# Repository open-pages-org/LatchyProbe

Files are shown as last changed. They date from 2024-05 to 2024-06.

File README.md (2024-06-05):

# Latchy Probe

A 3D printable alternative to the Omron TL-Q5MC2 inductive sensor commonly used on FDM printers for bed leveling.

Having a printer with no auto bed leveling is frustrating. While BL-Touch is a common choice, inductive probes are simple off-the-shelf items. Klicky and Unklicky probes can be printed but need magnets. What if there was an alternative that you could easily print and only needs a few parts that you probably already have?

The inspiration for this is the Klicky probe (and other similar devices) that have led the way. The objectives for this project are almost identical to the Klicky objectives [here](https://github.com/jlas1/Klicky-Probe/blob/main/README.md).

All the details, instructions and printable parts for the Latchy Probe are shared [here](https://github.com/open-pages-org/LatchyProbe) in Github, contributions to the project are welcome.

LatchyProbeVideo (https://www.youtube.com/watch?v=6NL-_C0w8O0) 

## Objectives
- Drop-in replacement for Omron TL-Q5MC2 or PL-08N2 (no need to replace the toolhead)
- No soldering required
- Minimal adjustments required
- Detect all print surfaces
- Close to the hotend tip
- Highly repeatable and accurate
- Less temperature variation
- No melting of parts
- Cheap to build
- Reuse spare parts if possible

## Additional Features
- Uses common items found at home, no special parts needed
- Does not reduce the printable area
- No detachable parts

The Latchy Probe has been developed over many months, with dozens of prototypes and 3 full test versions. It has been tested on a Creality CR10 (my Voron is still in the pipeline) and works well. The design is optimized for FDM printing but can be miniaturized using resin printing. Feedback is always welcome here or on Discord (crashysmashy1).

If you want to support this project, please consider donating [here](https://paypal.me/CrashySmashy?country.x=GB&locale.x=en_GB).

## Presenting the Latchy Probe
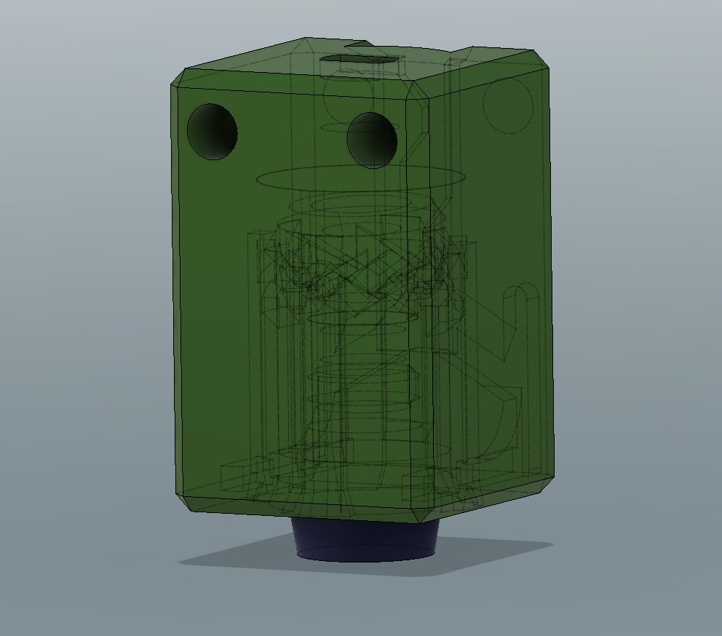
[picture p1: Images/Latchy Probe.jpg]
Latchy Probe


Latchy Probe is a direct size-for-size replacement for the Omron TL-Q5MC2 inductive probe, allowing it to use the same mounting points and adaptors for many printers.

### Features
- Physical contact switch of the same size as the inductive probe
- Deployed using the 3D printer’s motion system, like Klicky
- Similar internal contacts to Unklicky, but without detachable parts
- Probe tip retracts when not in use, similar to BLTouch
- Cheap, accurate, and can be built at home using parts from a retractable pen

Electrically, it uses only 2 wires that can be connected to the probe input on controller boards, with no external signals or power connections needed. The probe circuit is fail-safe, as it has a normally closed circuit when correctly deployed.

### Deployment
The probe is deployed by pressing the tip down onto a small post located on the printer frame to release the latch. 
- For a bed slinger the post can be at one end of the X axis.
- For Core XY the post can be near the Z homing pin.
The trigger post can be rigid or flexible, a flexible post allows for accidental horizontal contact between the probe and the post without incident.

Macros allow the deployment process to be automated. Example macros for deployment and retraction moves are provided [here](Macros/README.md). If the probe is not deployed before use, the probe circuit will remain open, and standard Klipper macros will report "Probe is already triggered" and stop.

## Building the Probe

### Parts Needed
- 3D printed parts
- Spring from a retractable pen, more details [here](#finding-a-spring)
- Thick copper wire for contacts (1.3mm diameter, 16AWG, 17SWG, or 18SWG)
- Connection wiring
- Mounting screws

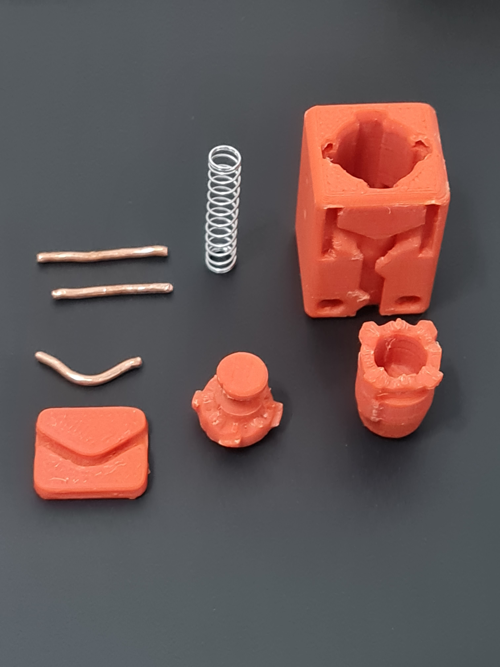
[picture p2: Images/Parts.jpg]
Latchy probe parts


### Printing the Parts
Ensure your printer is well-tuned to avoid issues like stringing, layer zits (if needed, paint the z seam into recessed corners), blobs, elephant foot, and over extrusion. 

Use the following settings:
- Print speed: Slow print speed with sufficient cooling
- Layer height: 0.1mm or 0.15mm
- Nozzle: 0.4mm (or finer if available)
- Material: ABS or ASA
- Supports: Not required
- Perimeters: 3
- Top/Bottom Layers: 5
- Infill: 15%

Parts to print:
- Probe Case (select the case to suit the available wire size)
- Probe (select the probe to suit the available wire size)
- Probe Latch
- Trigger Post, more details [here](#Trigger-Post-and-Mounting-Brackets)
- Optional bending and cutting jig for the cross pin

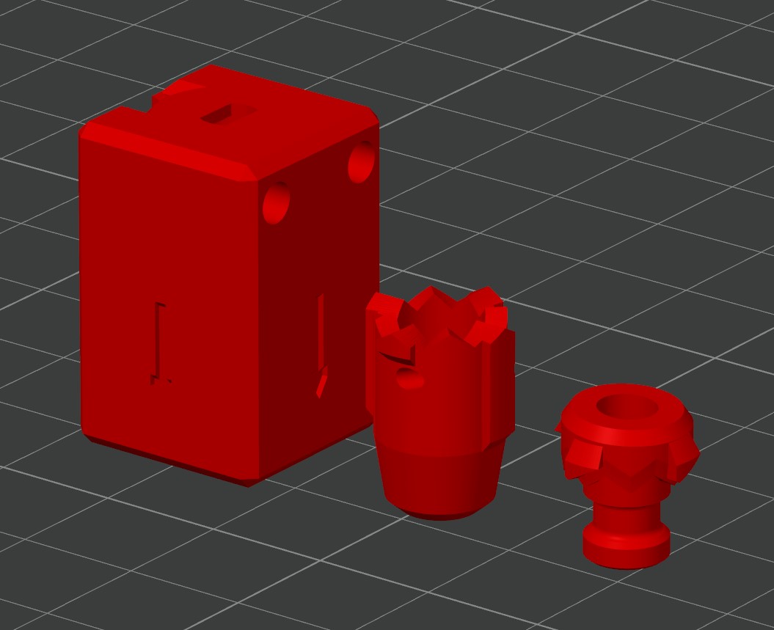
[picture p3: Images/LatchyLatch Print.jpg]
Latchy 3D prints


### Finding a Spring
- Spring diameter: 3-4.5mm (ideal size: 4.25mm)
- Spring length: approximately 23mm free length and 7mm compressed
- Spring force: 0.35mm wire diameter

If the spring is too soft the contacts will not be reliable. If the spring is too stiff it will displace the bed surface when probing giving inaccurate readings.

### Assembly
1. Cut 3 lengths of copper wire approximately 15mm long. Bend 1 piece to match the profile of the jig and trim the ends flush with the jig. Ensure there are no burrs and round the ends with a file if needed.

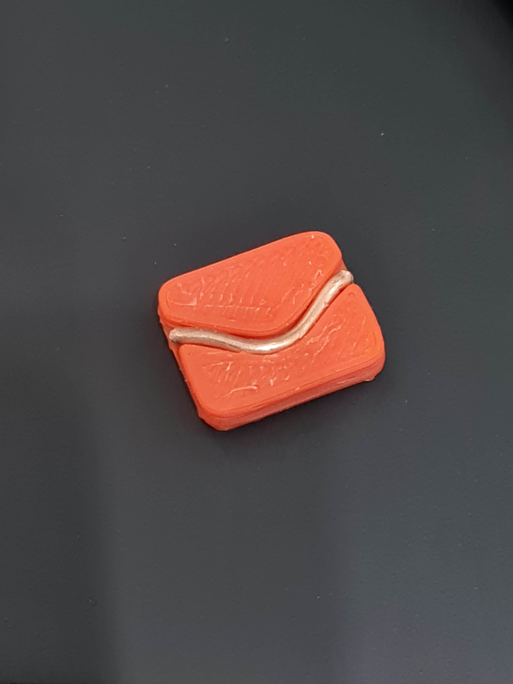
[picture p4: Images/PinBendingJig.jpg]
Pin bending jig


2. Insert the latch part into the probe part; the latch should rotate freely, bumping up and down on the ramps.

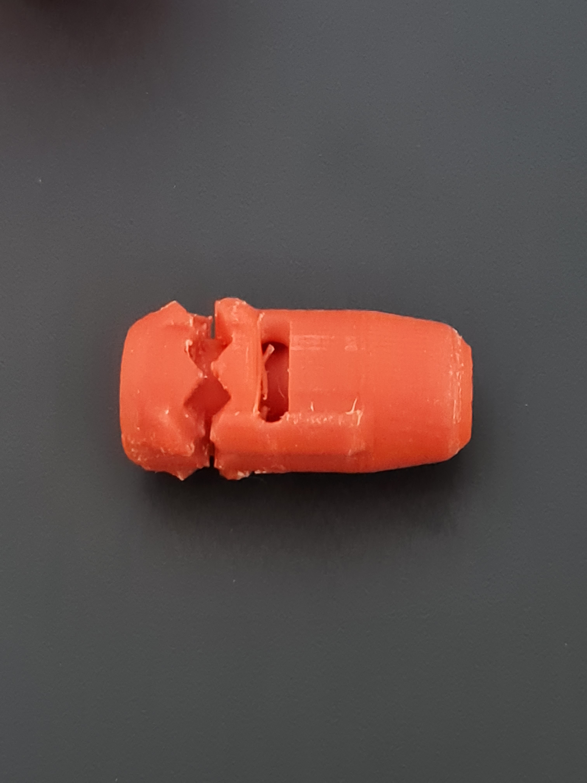
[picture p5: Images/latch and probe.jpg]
Latch and probe


3. Insert the copper cross pin (this retains the parts and forms the electrical contact). The latch should still rotate freely.

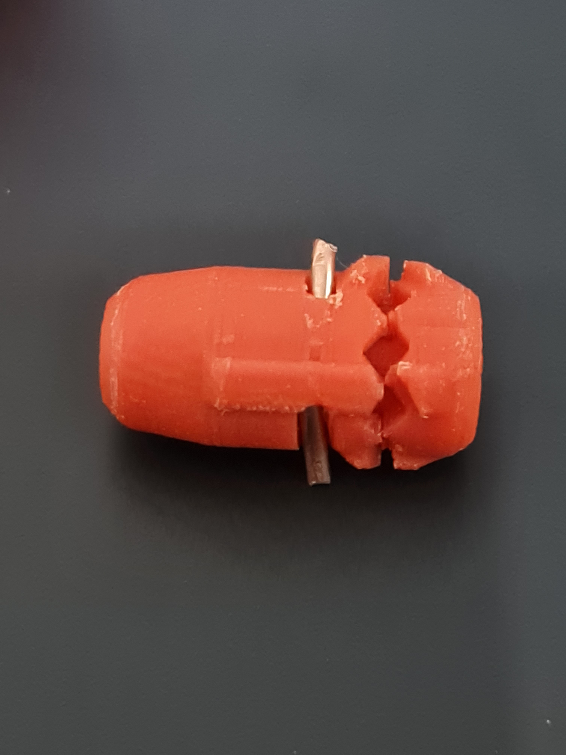
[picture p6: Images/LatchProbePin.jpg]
Latch in Probe with Pin


4. Insert the spring into the cup on the latch.

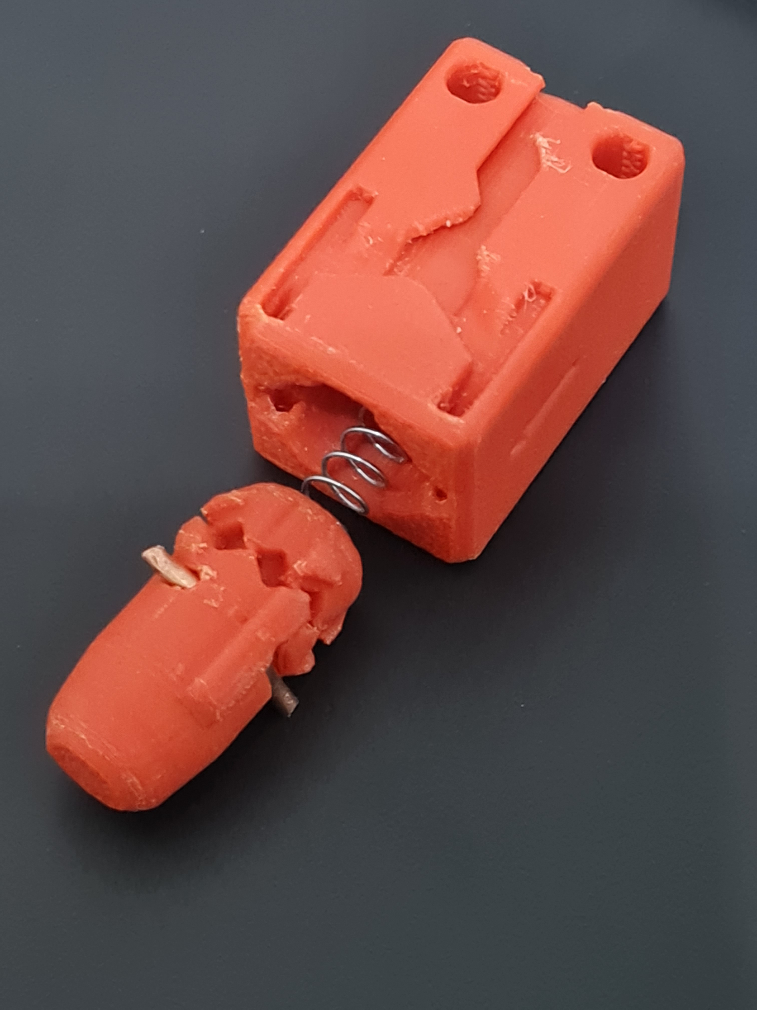
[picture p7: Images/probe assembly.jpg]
Probe assembly


5. Insert the assembly into the body and stand on end. The assembly should slide in and out smoothly for the first 5mm.

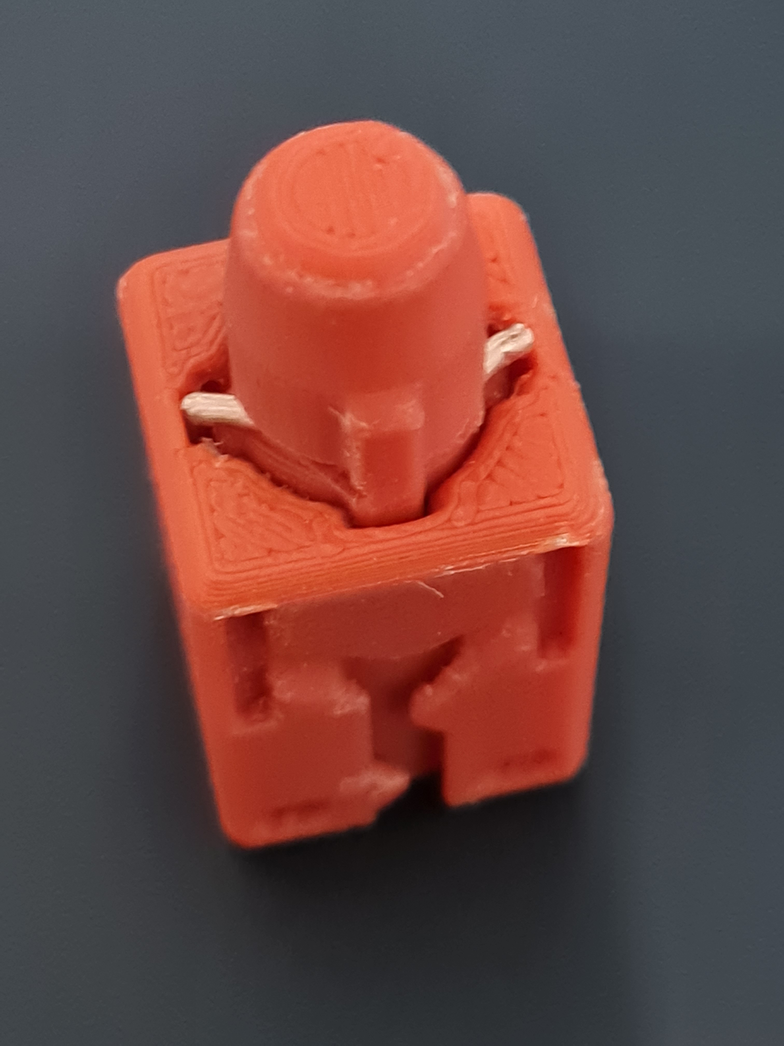
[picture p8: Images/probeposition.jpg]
Probe in initial position


6. Initial Testing: 

Press the assembly further into the body and it should latch in place. Press again and it should release. If the latch does not rotate smoothly, clean up the parts and sand lightly to reduce layer lines on the sliding surfaces.

7. Strip the connection wires back about 5 to 7mm.

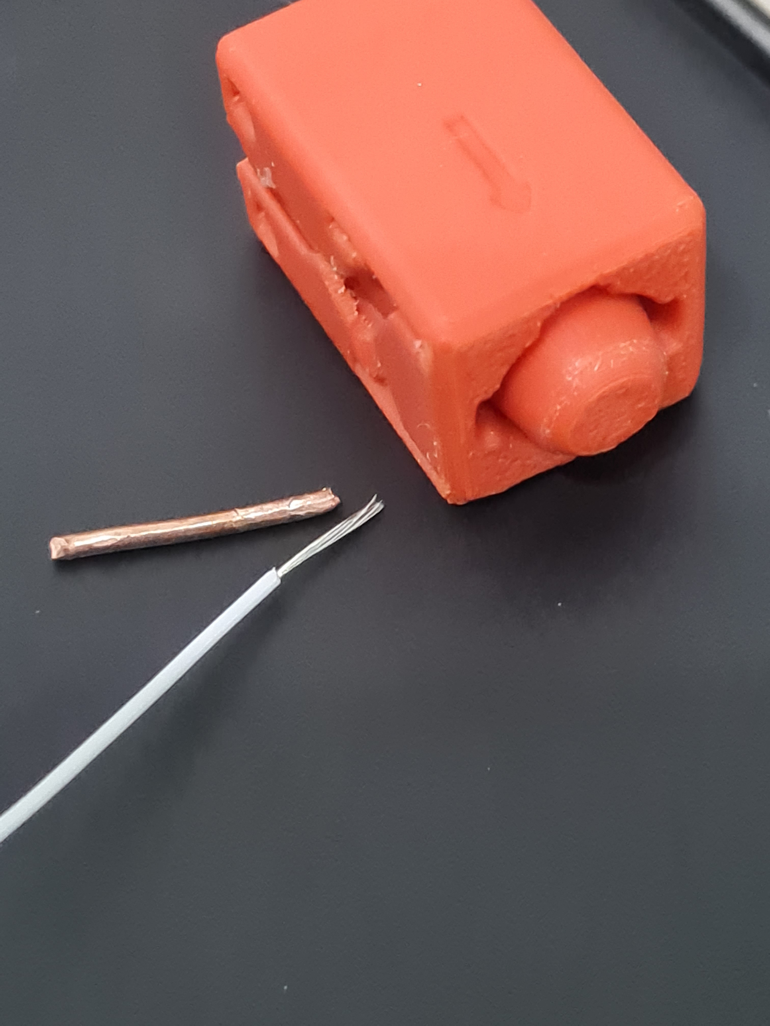
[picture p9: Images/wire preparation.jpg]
Wire preparation


8. With the probe inserted and latched, insert the connection wire into the body. Only insert the stranded wires, not the insulation.

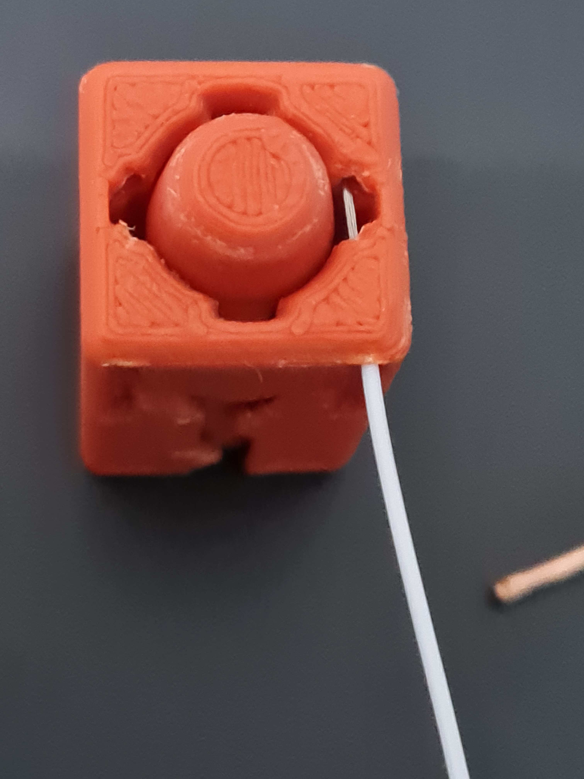
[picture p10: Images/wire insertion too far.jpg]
Wire insertion too far


9. Insert a copper pin approximately 10mm. It must grip the braided wires and extend across the slot to form the contact.

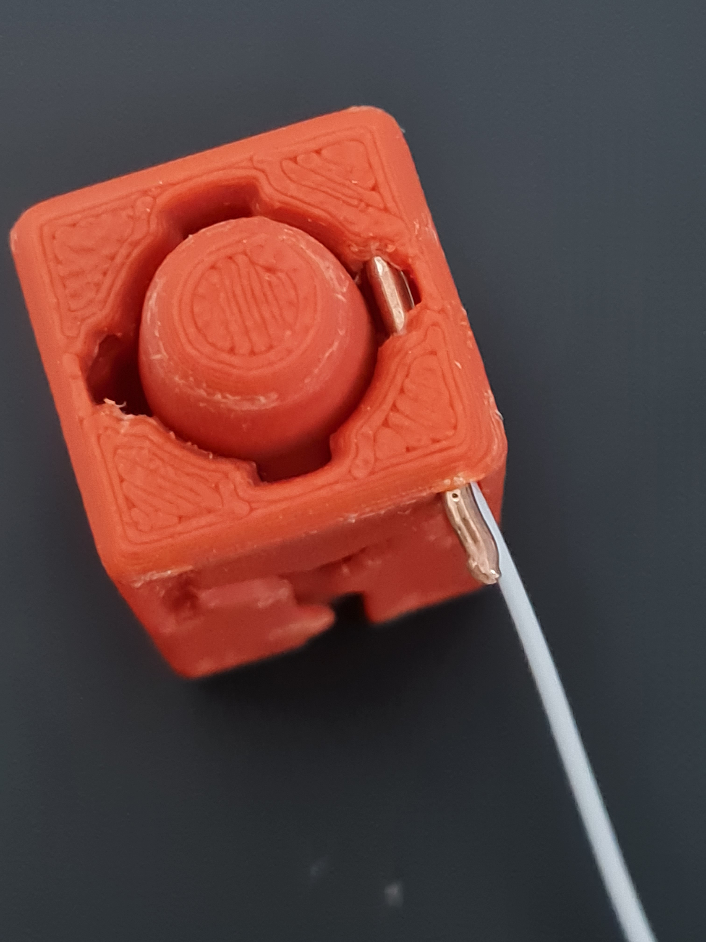
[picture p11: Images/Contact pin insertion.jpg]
Contact pin insertion


10. Bend the end of the copper pins down into the wire slot.

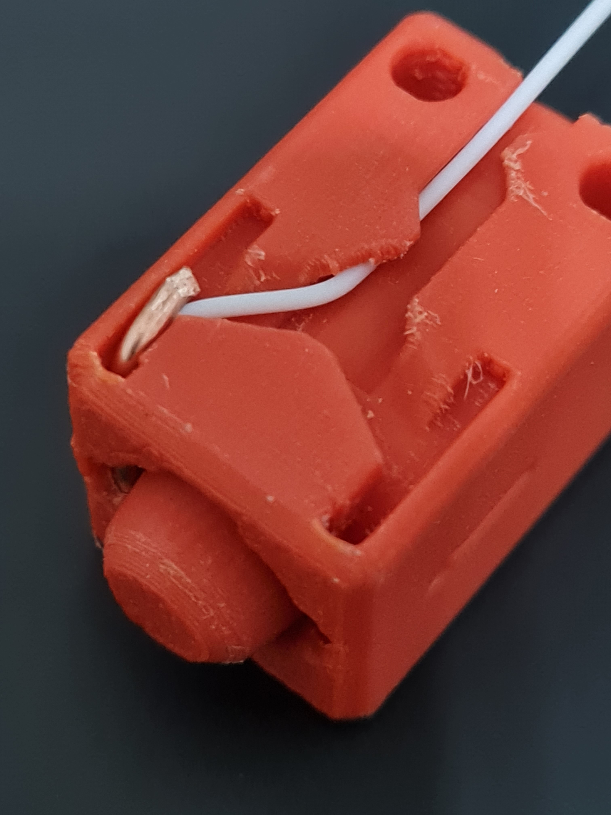
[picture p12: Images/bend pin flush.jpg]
Bend pin flush


11. Repeat step 7 with the second copper pin.

**Note 1**: Ensure both pins are the same diameter and sit evenly in the body for reliable contact.

**Note 2**: Alternatively, use a crimp pin from a JST socket.

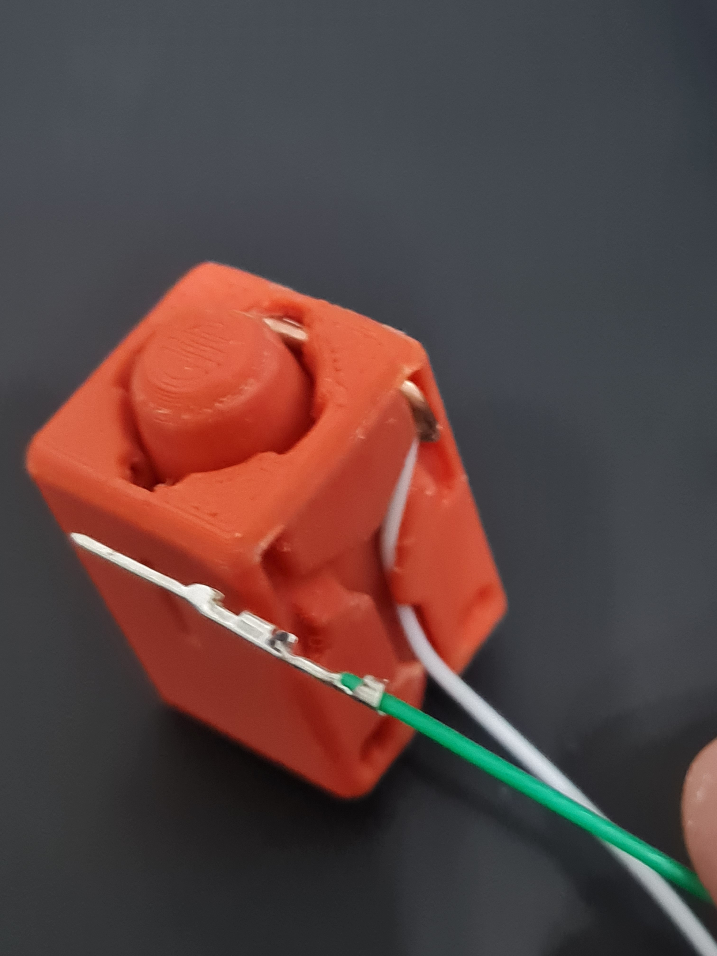
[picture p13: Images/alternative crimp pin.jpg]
Alternative crimp pin


12. Route the wires in the channel on the body.

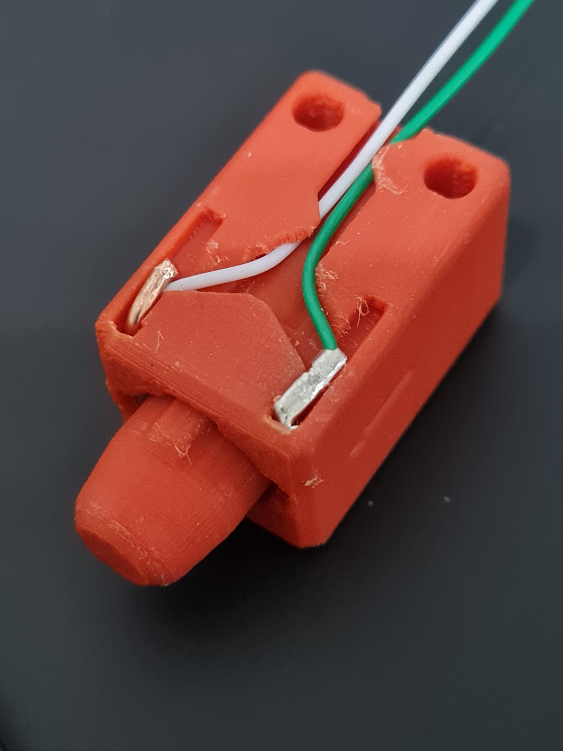
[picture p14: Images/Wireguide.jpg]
Wire guide


### Electrical Testing
Test electrical continuity. The circuit should be complete when the probe is extended. When the probe is pressed in a fraction of a mm, the circuit should open.

## Trigger Post and Mounting Brackets
The table below provides the list of currently avaialble trigger posts for various prointers. The trigger post needs to extend approximately 5mm above teh bed height to allow the probe to be deployed without the nozzle hitting the bed.

Measure the height from the frame to the bed and add 5mm. When printing, scale the triggger post STL file in Z direction so the height is correct.

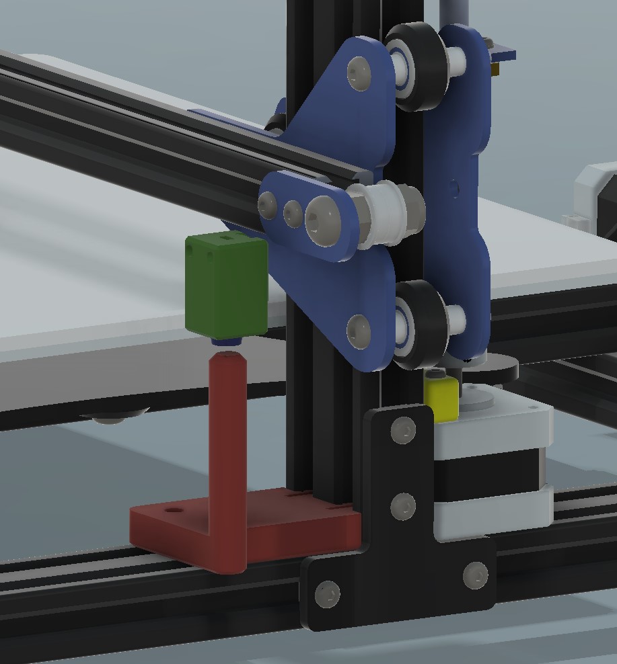
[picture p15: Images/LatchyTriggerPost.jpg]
Trigger post mounted to frame
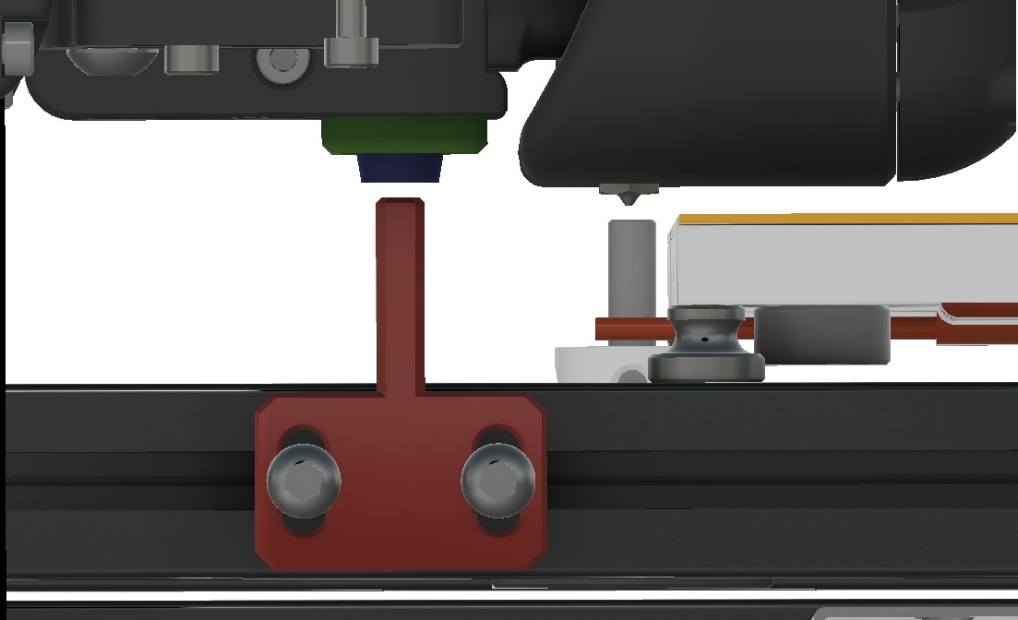
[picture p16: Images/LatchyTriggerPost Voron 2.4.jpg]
Trigger post mounted to Voron frame
 

If you need help designing a trigger post for your specific printer, let me know, and I can help create some standard parts. I welcome sharing of trigger posts and mounts submitted by users; please message me, and I will include them in the STL folders.

| Printer | Trigger Post and mountings | Notes |
|---|---|---|
| Creality CR10v2 | [Trigger post](STL/Trigger_Posts/) , [Mounting bracket](https://www.printables.com/model/135722-cr-10-v2-omron-tl-q5mc2-inductive-probe-mount) | The trigger post clips to the frame and can be secured with a T-nut and screw if required. |
| Voron 2.4 | [Trigger post V2.4](STL/Trigger_Posts/LatchyTriggerPost_Voron2.4.stl) | The trigger post is screwed to the frame using T-Nuts, print flat and scale in x or y if alternative height is needed. |
| Voron Trident | TBC | |

### Tools
- 3D Printer
- Multimeter to check for continuity
- Wire Cutters

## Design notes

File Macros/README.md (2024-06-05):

# Klipper macros
The example macros below are for the CR10v2, the positions will need to be changed to suit your printer configuration. These macros have been developed based on examples from Klicky, Unclicky, Euclid, etc., further printer examples will be added as they are developed.

The standard Klipper macros do not include the deployment and retraction of the probe so these actions can be added to macro as needing using the following format:

``` general format
[gcode_macro MACRO_NAME]
rename_existing: _MACRO_NAME # Renames the existing macro with and underscore prefix
gcode:
  PROBE_EXTEND  #Deploy the probe
  _MACRO_NAME #Call the original macro that was renamed
  PROBE_RETRACT  #Retract the probe
```

Homing the printer with the probe extended may damage the probe if it dragged sideways on the bed. Use 5mm z hop and home x and y first before homing z.

``` Safe Z Home
[safe_z_home]
home_xy_position: 0,0 # Change coordinates to the preferred location on your print bed
speed: 50
z_hop: 5 # Move up 5mm
z_hop_speed: 5
```

# The following macros control the probe deployment and motion
The movements to retract and extend the probe are identical however there are separate macros for PROBE_EXTEND and PROBE_RETRACT that check the status of the probe before performing the action. Note also, due to the way templates are evaluated, separate macros are needed for checking the status to the macros before performing actions.

For example, before running a bed mesh calibrate use Probe_Extend and then afterward use PROBE_RETRACT before printing.

The following macros are all needed and work together when using the probe. 
- PROBE_EXTEND
- PROBE_RETRACT
- MOVE_PROBE_CLEAR
- SET_PROBE
- CYCLE_PROBE

## Macro PROBE_EXTEND to prepare the probe ready for use
This will initiate all steps needed to use the probe.
```PROBE_EXTEND
[gcode_macro PROBE_EXTEND]
gcode:
  MOVE_PROBE_CLEAR # ensure the probe is not pressed in by the bed before checking status
  Query_Probe #get the current probe status
  SET_PROBE ACTION=extend
```
## Macro PROBE_RETRACT to retract the probe after use
This will retract the probe after use but can also be used after a printer restart or before printing to ensure the probe is retracted.
```PROBE_RETRACT
[gcode_macro PROBE_RETRACT]
gcode:
  MOVE_PROBE_CLEAR # ensure the probe is not pressed in by the bed before checking status
  Query_Probe #get the current probe status
  SET_PROBE ACTION=retract
```

## Macro MOVE_PROBE_CLEAR to move the head away from the bed before checking the probe
This makes sure the probe is not pressed so the Query_Probe result can be used to check the latched position of the probe. 
It also makes sure the printer is homed before using the probe.
```MOVE_PROBE_CLEAR
[gcode_macro MOVE_PROBE_CLEAR]
gcode:
  {% if not 'xyz' in printer.toolhead.homed_axes %}   # Check if already homed
      RESPOND MSG='Homing first'
      G28
  {% endif %}
  {% if printer.toolhead.position.z < 8 %}   # Check if the current Z position is less than 8mm
        RESPOND MSG="Current Z position: { printer.toolhead.position.z } - Moving up by 8mm"
        G91 ; Set to relative positioning
        G1 Z8 ; # Move up 8mm to clear probe extension which is approximately 6mm
        G90 ; Set back to absolute positioning
  {% endif %}
  RESPOND MSG="Current Z position: { printer.toolhead.position.z } - Probe is clear of bed"
```

## Macro SET_PROBE to set the probe to either retract or extend
This will check the current probe setting and call for the probe to be cycled if needed. 
Query_Probe must be used before this macro and then use 'SET_PROBE ACTION=retract' or 'SET_PROBE ACTION=extend'
```SET_PROBE
[gcode_macro SET_PROBE]
gcode:
  {% set probe_action = params.ACTION %}
  {% if probe_action == "extend" %}
      {% if printer.probe.last_query == 0 %}
        RESPOND MSG=" Probe is already extended! " ; Send message to console
      {% else %}
        RESPOND MSG=" Extending probe " ; Send message to console
        CYCLE_PROBE
      {% endif %}
  {% elif probe_action == "retract" %}
    {% if printer.probe.last_query == 1 %}
        RESPOND MSG=" Probe is already retracted! " ; Send message to console
    {% else %}
        RESPOND MSG=" Retracting probe! " ; Send message to console
        CYCLE_PROBE
    {% endif %}
  {% endif %}
  Query_Probe
 ```
       
 ## Macro CYCLE_PROBE to push the probe onto the trigger post to retract or extend
 This will cycle the probe from one state to the other.
```CYCLE_PROBE
[gcode_macro CYCLE_PROBE]
gcode:
  {% if not 'xy' in printer.toolhead.homed_axes %}   # If x and y are not homed
      { action_raise_error("Must Home X and Y Axis First!") }
  {% endif %}
  G90 # Set absolute positioning
  G1 Z20 # set Z height clear of trigger post
  G1 X310 F4000 # move x position over trigger post (include y position if needed)
  G1 Z3.5 # move Z down to the latching point (obtain this value by setting the probe over the trigger post and jogging z down until the click is heard and subtract 0.5mm for reliability)
  G4 P100 Pause
  G1 Z20 # set Z height clear of trigger post
  G4 P100 Pause
  G1 X100 F4000 # move x position to middle of bed or other preferred start point
```

# Modifications to standard Klipper macros
The following macros modify the existing macros to include the EXTEND and RETRACT macros.

## Macro for bed mesh calibrate
```BED_MESH_CALIBRATE
[gcode_macro BED_MESH_CALIBRATE]
rename_existing: _BED_MESH_CALIBRATE
gcode:
  PROBE_EXTEND
  _BED_MESH_CALIBRATE
  PROBE_RETRACT
```

## Macro for probe callibration
```PROBE_CALIBRATE
[gcode_macro PROBE_CALIBRATE]
rename_existing: _PROBE_CALIBRATE
gcode:
  PROBE_EXTEND
  G90
  G1 Z20
  G1 X115 Y115 F20000
  _PROBE_CALIBRATE
  TESTZ Z=20
  PROBE_RETRACT
```

## Macro for checking the probe accuracy
```PROBE_ACCURACY
[gcode_macro PROBE_ACCURACY]
rename_existing: _PROBE_ACCURACY
gcode:
  PROBE_EXTEND
  G90
  G1 Y115 X115 F20000
  _PROBE_ACCURACY
  PROBE_RETRACT
```

## Macro for adjust z tilt 
Note, this is if you have a setup that allows independent control of z motors, this does not apply for CR10v2.
```Z_TILT_ADJUST
[gcode_macro Z_TILT_ADJUST]
rename_existing: _Z_TILT_ADJUST
gcode:
PROBE_EXTEND
Z_TILT_ADJUST
PROBE_RETRACT
```

# Printer and probe configuration details
The following configurations also need to be added to Printer.cfg when adding a probe

# Configuration of the probe
This is based on the configuration for the CR10v2, change the settings for other printers
``` CR10v2 Probe configuration
[probe]
pin: ^PD2 #Probe pin for CR10v2 2.5.2 Board (Uses the BLTouch connections)
x_offset: 50 #probe to nozzle x distance
y_offset: -3.4 #probe to nozzle y distance
#z_offset: -6 #probe to nozzle z distance, this gets overwritten by the calibration macro
speed: 5
lift_speed: 50.0
samples:2
samples_result: median
sample_retract_dist: 1.0
samples_tolerance: 0.01
samples_tolerance_retries: 6
```

## Configuration for the bed mesh settings
Change the setting for mesh size and coverage to suit your printer.
``` bed mesh configuration
[bed_mesh]
speed: 100
horizontal_move_z: 5  #Height of the Z above the bed during the horizontal moves between points
mesh_min: 50,5
mesh_max: 250,290
probe_count: 5,5
algorithm: bicubic
fade_start: 1
fade_end: 10
#fade_target:
#   The z position in which fade should converge. When this value is set
#   to a non-zero value it must be within the range of z-values in the mesh.
#   Users that wish to converge to the z homing position should set this to 0.
#   Default is the average z value of the mesh.
split_delta_z: 0.015
#   The amount of Z difference (in mm) along a move that will
#   trigger a split. Default is .025.
move_check_distance: 3
#   The distance (in mm) along a move to check for split_delta_z.
#   This is also the minimum length that a move can be split. Default
#   is 5.0.
mesh_pps: 4,4
#   A comma separated pair of integers (X,Y) defining the number of
#   points per segment to interpolate in the mesh along each axis. A
#   "segment" can be defined as the space between each probed
#   point. The user may enter a single value which will be applied
#   to both axes.  Default is 2,2.
#bicubic_tension: .2
#   When using the bicubic algorithm the tension parameter above
#   may be applied to change the amount of slope interpolated.
#   Larger numbers will increase the amount of slope, which
#   results in more curvature in the mesh. Default is .2.
```

## Configuration for bed screw tilt adjustment
This is used when measuring the bed height above each corner screw for manual adjustment. Change the X, Y positions and screw thread type to suit your printer.
``` screw tile adjust
[screws_tilt_adjust]
screw1: 0,29
screw1_name: front left screw
screw2: 228,29
screw2_name: front right screw
screw3: 228,269
screw3_name: rear right screw
screw4: 0,269
screw4_name: rear left screw
speed: 50
horizontal_move_z: 10
screw_thread: CW-M3
```

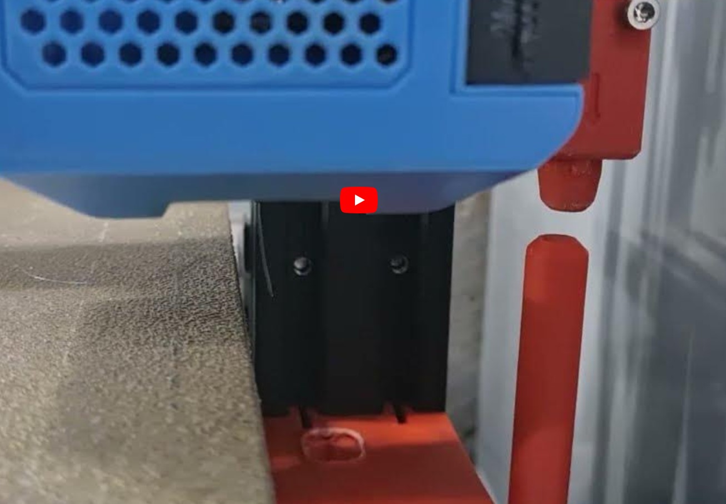
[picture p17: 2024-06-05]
Images/VideoThumbnail.jpg

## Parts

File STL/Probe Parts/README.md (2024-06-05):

# STLs

There are 2 versions of some STLs that can be chosen to suit the wire size avaialble for the pins. 

There is no difference in function and the minimum printing needed is 1 case, 1 latch and 1 probe

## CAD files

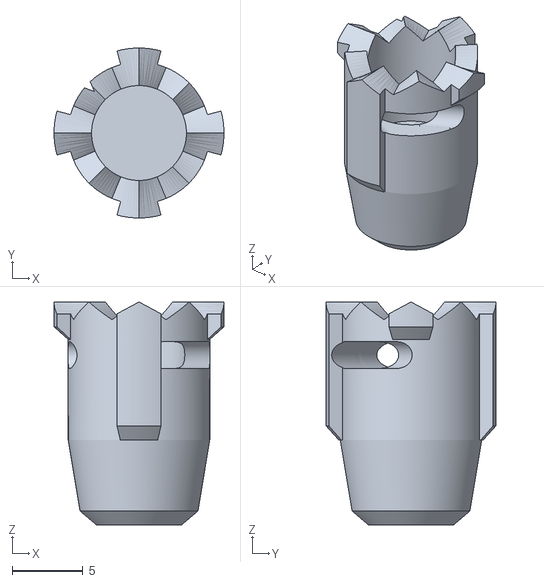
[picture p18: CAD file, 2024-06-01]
STL/Probe Parts/LatchyProbe ThickWire.stl
12.0 x 12.0 x 15.8

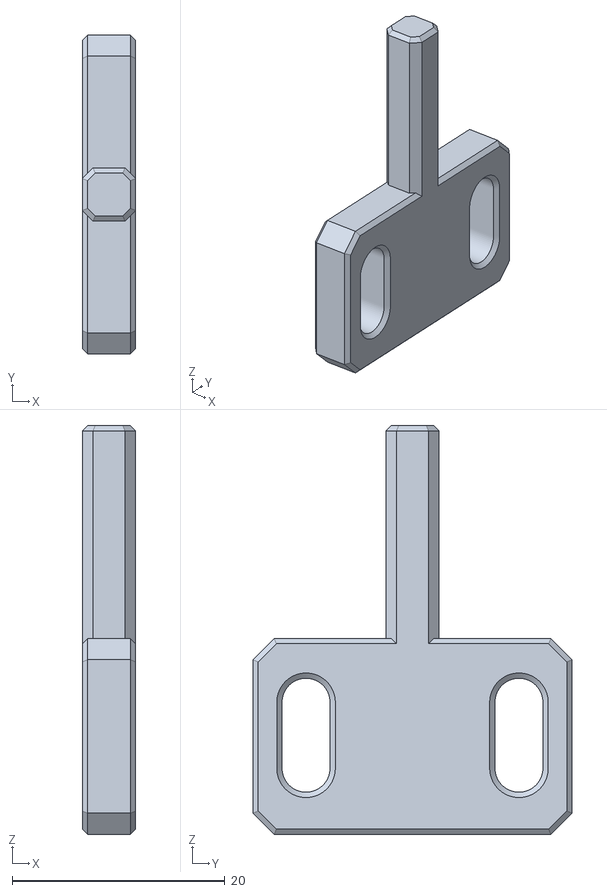
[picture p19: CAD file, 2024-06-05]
STL/Trigger_Posts/LatchyTriggerPost_Voron2.4.stl
5.00 x 30.0 x 38.4

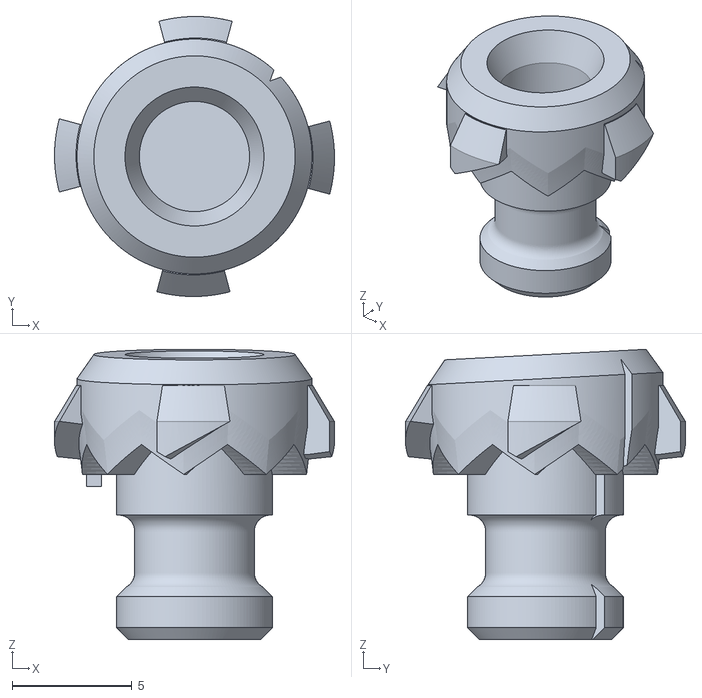
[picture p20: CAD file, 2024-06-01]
STL/Probe Parts/LatchyLatch.stl
11.7 x 11.7 x 12.1

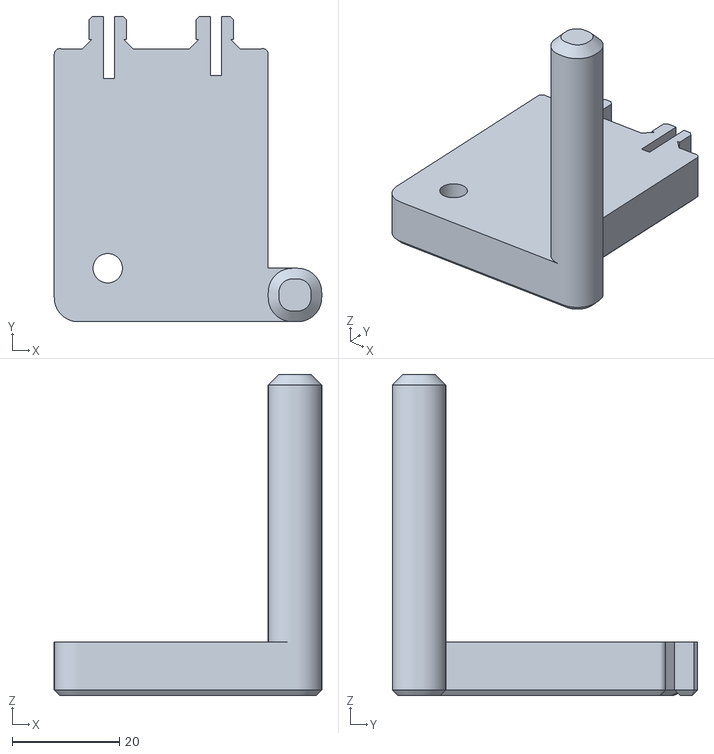
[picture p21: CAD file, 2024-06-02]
STL/Trigger_Posts/LatchyTriggerPost_CR10v2.stl
50.0 x 57.1 x 60.0

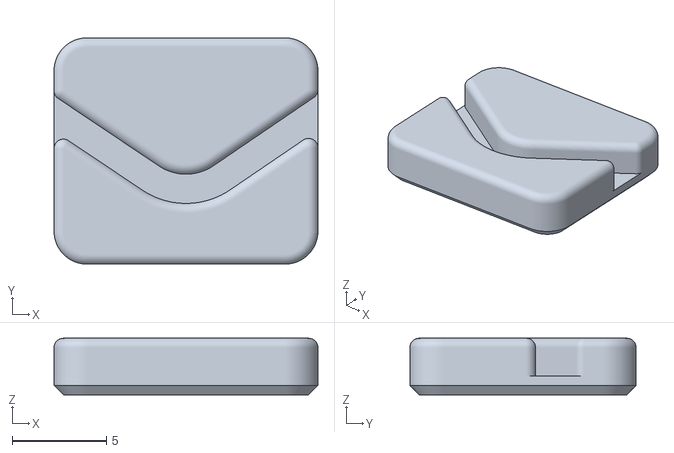
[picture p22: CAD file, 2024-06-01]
STL/Probe Parts/LatchyPinJig.stl
14.0 x 12.0 x 3.00

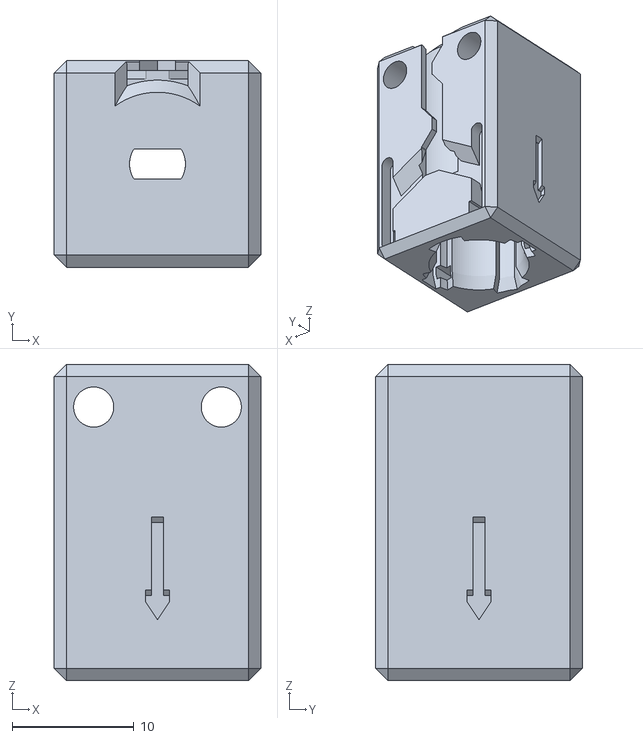
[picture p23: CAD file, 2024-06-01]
STL/Probe Parts/LatchyCase Thin Wire.stl
17.0 x 17.0 x 26.0

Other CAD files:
STL/Probe Parts/LatchyCase ThickWire.stl
STL/Probe Parts/LatchyProbe ThinWire.stl

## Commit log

2024-05-31 Rename Latchy Probe.jpg to Images/Latchy Probe.jpg
2024-06-01 Rename 20240514_231026.jpg to latch and probe.jpg
2024-06-01 Rename 20240514_231116.jpg to probe assembly.jpg
2024-06-01 Rename 20240514_233201.jpg to wire preparation.jpg
2024-06-01 Rename 20240514_233235.jpg to wire insertion too far.jpg
2024-06-01 Rename 20240514_233418.jpg to Contact pin insertion.jpg
2024-06-01 Rename 20240514_233916.jpg to alternative crimp pin.jpg
2024-06-01 Rename 20240514_233523.jpg to bend pin flush.jpg
2024-06-01 Rename LatchyProbe ThinWire.stl to STL/LatchyProbe ThinWire.stl
    [LatchyProbe ThinWire.stl]
2024-06-02 Rename STL/LatchyTriggerPost-CR10v2.stl to STL/Trigger Posts/LatchyTriggerPost-CR10v2.stl
    [LatchyTriggerPost-CR10v2.stl]
2024-06-02 Rename STL/LatchyCase ThickWire.stl to STL/Probe Parts/LatchyCase ThickWire.stl
    [LatchyCase ThickWire.stl]
2024-06-02 Rename STL/LatchyCase Thin Wire.stl to STL/Probe Parts /LatchyCase Thin Wire.stl
    [LatchyCase Thin Wire.stl]
2024-06-02 Rename STL/LatchyLatch.stl to STL/Probe Parts/LatchyLatch.stl
    [LatchyLatch.stl]
2024-06-02 Rename STL/LatchyPinJig.stl to STL/Probe Parts/LatchyPinJig.stl
    [LatchyPinJig.stl]
2024-06-02 Rename STL/LatchyProbe ThickWire.stl to STL/Probe Parts/LatchyProbe ThickWire.stl
    [LatchyProbe ThickWire.stl]
2024-06-02 Rename STL/LatchyProbe ThinWire.stl to STL/Probe Parts/LatchyProbe ThinWire.stl
    [LatchyProbe ThinWire.stl]
2024-06-02 Rename LatchyCase Thin Wire.stl to LatchyCase Thin Wire.stl
    [LatchyCase Thin Wire.stl]
